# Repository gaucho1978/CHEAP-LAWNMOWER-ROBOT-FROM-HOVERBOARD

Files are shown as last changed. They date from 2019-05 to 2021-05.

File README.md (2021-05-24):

You can control this lawnmower robot with a rc radiocontrol like a big rover, or let it automatically take care of your garden.
You could also replace the radiocontrol with bluetooth receiver conneted on the slave board serial line (reference about this on Florian repository)

The main feature of this lawnmower, with reference to other lawnmower robot products, is that it is able to do its work without a perimeter wire. Compared to other cheap products, it has bigger battery so it is able to take care of really big garden.

Every 24 hours it cuts the garden grass then it returns to the charging station. 

It uses proximity sensors to avoid obstacles and for safety against blade touching (they reveal the distance of the robot from the ground in case someone tries to lift it, in order to stop the blade).

It moves with reference to the start point (the place where the ground station is) knowing which path to follow (i'm planning to save inside the robot the garden morphology or the path) in order to avoid the need of perimeter wire. 
The project is in progress. 

On 12 may 2019 it can only move with rc commands cause iM waiting to receive the sensors and the chassis.

------------------------------
#### MECHANICAL CONSIDERATIONS

The mechanical project is located in the folder LawnMowerMechanicalProject.
These are some images (the base is aluminium and the cover in polycarbonate):
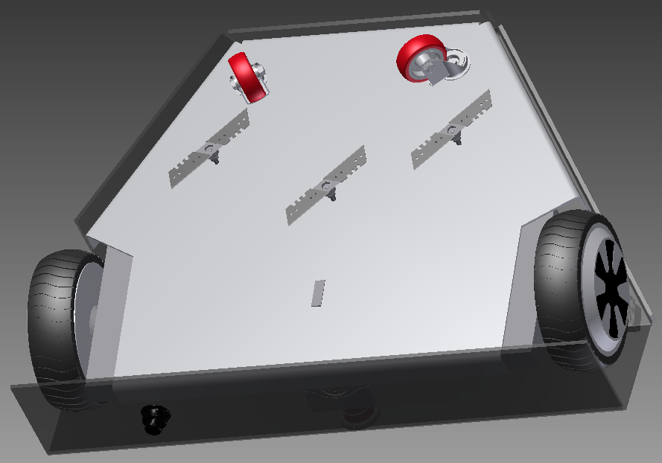
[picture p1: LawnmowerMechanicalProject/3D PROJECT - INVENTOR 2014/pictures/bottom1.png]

otter
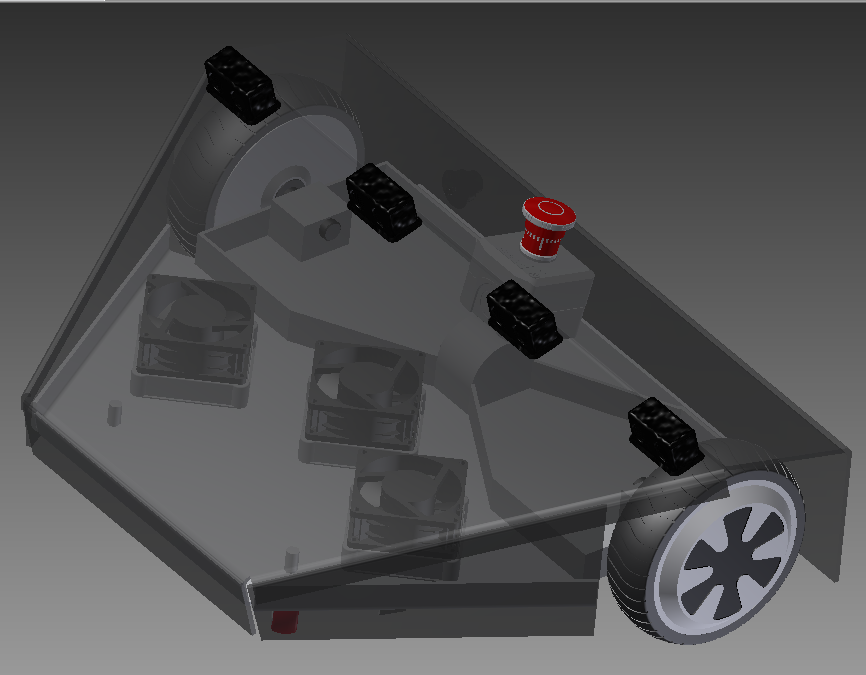
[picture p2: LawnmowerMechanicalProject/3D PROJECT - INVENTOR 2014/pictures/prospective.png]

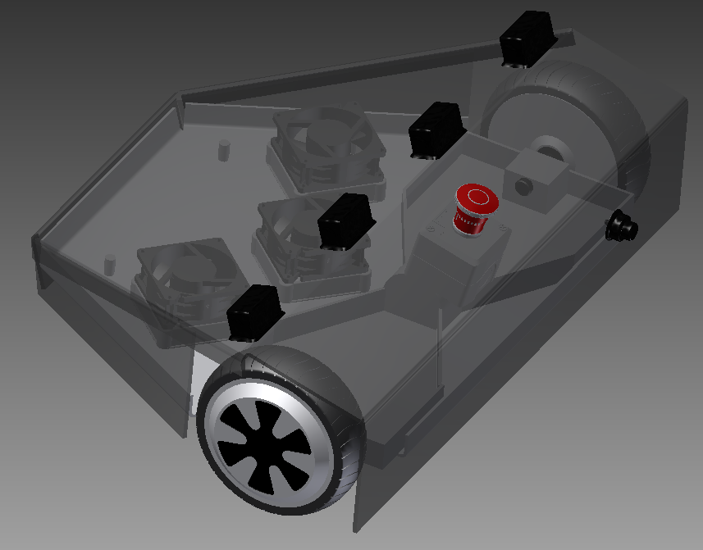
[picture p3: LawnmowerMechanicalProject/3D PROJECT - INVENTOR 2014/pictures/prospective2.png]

otter

- You will find files for manufacturing alluminium plate and polycarbonate cover in the folder:
   LawnMowerMEchanicalProject/FILES FOR MANUFACTURING/PDF FORMAT
- You will fing files for manufacturing plastic supports with 3d printer in the folder:
   LawnMowerMEchanicalProject/FILES FOR MANUFACTURING/3DPrinted supports
- The blade support shall be 3d printed. look ad detailed mechanical drawing to see how to assemble 3dprinted parts.

------------------------------
#### BILL OF MATERIAL - TOTAL COST around 160 EURO
50 EURO - USED HOVERBOARD - https://www.mediaworld.it/product/p-742077/i-bike-kidplay-streetboard-one-hoverboard-6-5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

20 EURO - TURNIGY 9X RADIOCONTROL OR ANY OTHER TYPE OF RC WITH PWM OUTPUT WITH AT LEAST 2 CHANNELS (ONE FOR SPEED AND ONE FOR STEERING)

6 EURO - STLINK V2 PROGRAMMER (TO FLASH HOVERBOARD FIRMWARE) - https://www.ebay.it/itm/352654456738?ViewItem=&item=352654456738

17 EURO - 10 PROXIMITY SENSORS HC-SR04 - https://www.ebay.it/itm/312495306039 https://www.amazon.it/dp/B07MPZR59P/ref=cm_sw_r_cp_apa_glt_i_Q1WTGSVRN5MXQZJ7DQEB?_encoding=UTF8&psc=1

2 EURO - Arduino nano(clone): https://www.ebay.it/itm/322913230315

1 EURO - DCDC(FOR ARDUINO AND/OR BLADE MOTOR): https://www.ebay.it/itm/122201239217

30 EURO - MOTORS FOR BLADES (I REUSED SOME 24V FAN, powering them with modified notebook AC/DC)

30 EURO - 3D PRINTED SUPPORTS FOR BEARING, (I PRINTED THEM FOR FREE WITH MY PRINTER)

1 EURO - FOUR BLADES FOR CUTTER (I FOUND THEM IN A LOCAL HARDWARE STORE (OBI))

10 EURO - POLYCARBONATE OR PLEXIGLASS COVER (I FOUND PIECE OF POLYCARBONATE FOR FREE )

10 EURO - ALUMINIUM OR IRON BASE (I FOUND ALUMINIUM PLATE FOR FREE)

5 EURO - SCREWS AND BOLTS

5 EURO - TWO ROTATING WHEELS 66mm HEIGHT (I FOUND THEM IN A LOCAL CHINESE SHOP)

2 EURO - PANIC BUTTON - https://www.ebay.it/itm/Rosso-fungo-Cap-1-NO-1-NC-ferma-emergenza-Pulsante-interruttore-DPST-660V-10A/123270871363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

------------------------------
#### HOVERBOARD HARDWARE
The hoverboard with 2 boards uses processor GD32F130C8 (instead of STM32F103 used on Niklas hoverboard) 
otter

The hoverboard hardware has two main boards, which are different equipped. They are connected via USART. Additionally there are some LED PCB connected at X1 and X2 which signalize the battery state and the error state. There is an programming connector for ST-Link/V2 and they break out GND, USART/I2C, 5V on a second pinhead.

The reverse-engineered schematics of the mainboards can be found in the folder HoverboardSchematics

In order to use  GPIO represented as "not used" on the hoverboard schematic, you need to solder some zero ohm resistors (or jumpers) (see schematic).

I soldered resistive dividers directly on the pcb as shown on the following image (while on the dwg lawnmower schematic, the resistors are represented as external components). this way the connection to the rc receiver becomes simple as few wires:
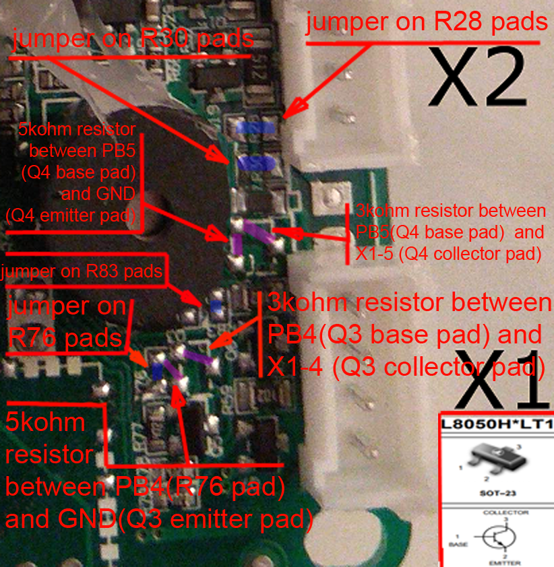
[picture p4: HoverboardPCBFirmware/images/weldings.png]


I REUSED THE HOVERBOARD HARDWARE AS IT IS. I DIDN'T MODIFIED THE FRAME, I JUST ROTATED IT 180 DEGREES.

------------------------------
#### HOVERBOARD FIRMWARE
I started my code from Florian Repository ( https://github.com/flo199213/Hoverboard-Firmware-Hack-Gen2 )

Florian rewrote the firmware for hoverboards composed by 2 boards, starting from Niklas repository ( https://github.com/NiklasFauth/hoverboard-firmware-hack/ )

Niklas rewrote the firmware for hoverboards composed by a big board and sensor boards.

First thing that I've done was to add PWM input to control the robot with a RC receiver, in order to let me do all the functional checks, before to implement automatic navigation algorithm.
I used turnigy rc receiver directly connected to the board, on the unused gpio.

Second thing that i've done was to add PWM output in order to control a ESC connected to a motor. The motor is connected to a blade. 

Every time the robot moves, the blade starts to rotate at constant speed.

The following image shows how the 3 phases changes during rotation. 

Note: A complete rotation of the phases is not a complete rotation of the wheel since there are many inductors inside the motor. 
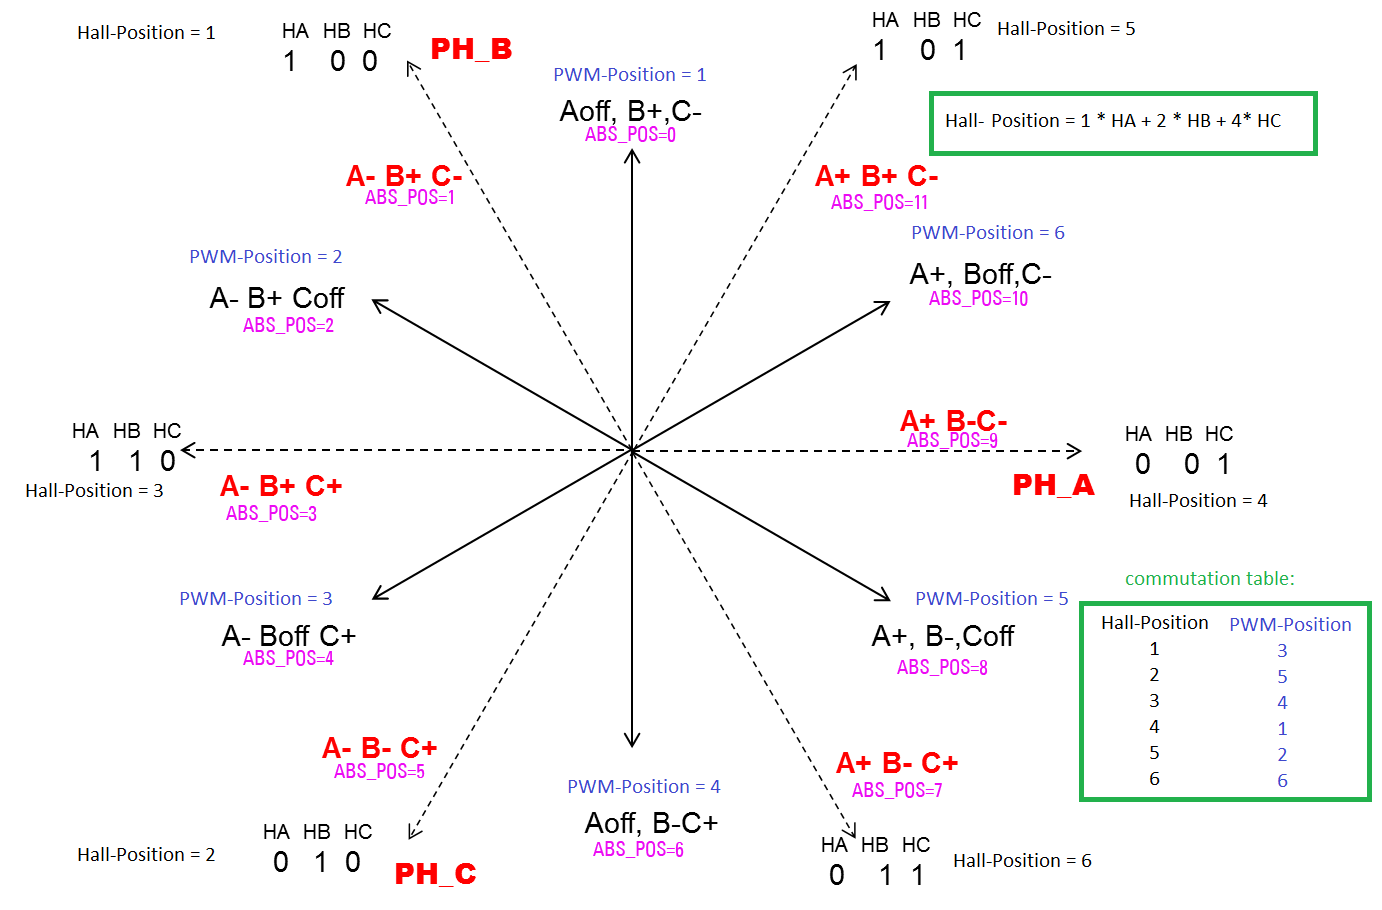
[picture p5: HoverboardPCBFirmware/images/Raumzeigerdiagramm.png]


FIRMWARE STRUCTURE:

-THE FILE "DEFINES" AND "CONFIG" CONTAINS MAIN PARAMETERS 

-THE FILE "IT" CONTAINS TIMING FUNCTIONS AND INTERRUPTS (PERIODIC CHECKS,  SERIAL LINE INTERRUPTS, SYSTEM TICKS)

-THE FILE "BDLC" CONTROLS THE HOVERBOARD MOTORS

-THE FILE "COMMSSTEERINGPWM" RECEIVES THE RC PWM SIGNALS TO MOVE THE HOVERBOARD IN SPEED AND DIRECTION.

-THE FILE "COMMSMASTERSLAVE" SENDS AND RECEIVE DATA BETWEEN MASTER AND SLAVE BOARD

-THE FILE "LED" CONTROLS THE GPIO OUTPUT GENERALLY CONNETED TO LEDS TO SHOW BATTERY STATUS ETC,ETC.

-THE FILE "COMMSACTUATOR"GENERATES THE PWM USED TO CONTROL THE MOTOR CONNECTED TO THE BLADE.

-THE FILE "MAIN" IS THE MAIN LOOP OF THE HOVERBOARD FIRMWARE THAT CALLS ALL THE ROUTINES IN SEQUENCE.

------------------------------
#### FLASHING
The firmware is built with Keil (free up to 32KByte). To build the firmware, open the Keil project file which is includes in repository. On the board, close to ARM processor, there is a debugging header with GND, 3V3, SWDIO and SWCLK. Connect GND, SWDIO and SWCLK to your SWD programmer, like the ST-Link V2.

- If you never flashed your mainboard before, the controller is locked. To unlock the flash, use STM32 ST-LINK Utility or openOCD.
- To flash the processor, use the STM32 ST-LINK Utility as well, ST-Flash utility or Keil by itself.
- Hold the powerbutton while flashing the firmware, as the controller releases the power latch and switches itself off during flashing

NOTE: I USE TO UNPLUG THE HOVERBOARD BATTERY AND TO PLUG THE STLINK PROGRAMMER (INCLUDED 3,3VOLT PIN), THEN TO FLASH THE FW USING KEIL. THIS WAY YOU DON'T NEED TO LEAVE PRESSED THE POWER BUTTON.

NOTE2: ONE BOARD IS MASTER THE OTHER IS SLAVE. BEFORE TO FLASH THE FW, SET THE FIRMWARE AS MASTER OR SLAVE IN THE CONFIG.H AND RECOMPILE THE FIRMWARE.

------------------------------
#### COMMUNITY
there is a Telegram group as a free discussion platform about Hoverboards MODS. You can find it here: https://t.me/joinchat/BHWO_RKu2LT5ZxEkvUB8uw

------------------------------
#### NEXT THINGS THAT I WILL DO: 
- add sensors and interlocks to algorithm,
- create a docking station for automatic recharge, 
- realize the mechanical structure, 
- implement safety for automatic stopping blade 
- implement automatic navigation algorithm.

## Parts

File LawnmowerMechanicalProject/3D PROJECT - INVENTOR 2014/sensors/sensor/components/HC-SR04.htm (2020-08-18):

Autodesk Inventor Translation Report | domenica 12 aprile 2020 (13:39)
Source File: | C:\Users\GauchoHP\Downloads\HC-SR04.stp
Translator Type: | STEP | Sending System: | DEX
Author: | Unknown | Translation Time: | 00:00:09
Options
Import Type: | N/A
Entity Types to Import: | Solids, Surfaces, Wires, Points
Import into Repair Environment: | Yes
Import Assembly as Single Part: | No
Create Surfaces As: | Single Composite Feature
Check Parts during Load: | No
Auto Stitch: | No
Enable Advanced Healing: | N/A
+/- | Name | Inventor File | Status
[ ] | HC-SR04.iam | C:\Users\GauchoHP\Downloads\Imported Components\HC-SR04\HC-SR04.iam | Successful
[+] [-] | Board.ipt | C:\Users\GauchoHP\Downloads\Imported Components\HC-SR04\Board.ipt | Warning
Severity | Entity Id | Message
Warning | 64531 | Some Surfaces have been simplified
[ ] | SOT23.ipt | C:\Users\GauchoHP\Downloads\Imported Components\HC-SR04\SOT23.ipt | Successful
[+] [-] | SOIC16 narrow.ipt | C:\Users\GauchoHP\Downloads\Imported Components\HC-SR04\SOIC16 narrow.ipt | Warning
Severity | Entity Id | Message
Warning | 260 | Some Surfaces have been simplified
[ ] | Crystal Oscillator (SMD).ipt | C:\Users\GauchoHP\Downloads\Imported Components\HC-SR04\Crystal Oscillator (SMD).ipt | Successful
[+] [-] | 0603 Resistor.ipt | C:\Users\GauchoHP\Downloads\Imported Components\HC-SR04\0603 Resistor.ipt | Warning
Severity | Entity Id | Message
Warning | 259 | Some Surfaces have been simplified
Warning | 259 | Sliver faces have been removed
[ ] | 0603 Capacitor.ipt | C:\Users\GauchoHP\Downloads\Imported Components\HC-SR04\0603 Capacitor.ipt | Successful
[ ] | Transducer.ipt | C:\Users\GauchoHP\Downloads\Imported Components\HC-SR04\Transducer.ipt | Successful
[ ] | Mesh.ipt | C:\Users\GauchoHP\Downloads\Imported Components\HC-SR04\Mesh.ipt | Successful

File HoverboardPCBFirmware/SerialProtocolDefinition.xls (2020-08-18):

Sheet: Messages
Direction | Byte Count | 0 | 1 | 2 | 3 | 4 | 5 | 6 | 7 | 8 | 9 | 10 | Note
Remote Serial Port → Master Board | 3-:-9 | / | cmd | ± | Value |  |  |  |  | \r |  |  | This message uses only ASCII characters and it is used as debug port Bytes from 2 to 7 are optional, used only in movement commands cmd: See CMD LEGEND sheet
 |  | char | char | char | char1 | char2 | char3 | char4 | char5 | char
Master Board→ Remote Serial Port | for returned message see CMD LEGEND sheet
Master Board→ Slave Board | 10 | / | SPEED |  | ID | VALUE |  | Bits | CRC |  | \n |  | SPEED: is the SPEED value in mm/sec to set on the Slave motor Identifier+Value: See ID Legend sheet Bits: See Bits Legend sheet CRC: checksum of the transmitted data
 |  | char | int16 |  | uint8 | int16 |  | uint8 | uint16 |  | char
Slave Board → Master Board | 5 | / | Bits | CRC |  | \n
 |  | char | uint8 | uint16 |  | char
Slave Board→ Remote Serial port | 11 | / | ID |  | 0 | ± | Value |  |  |  |  | \n | ID, ReadWrite and VALUE are ascii characters. ID: from 00 to 99 (see ID Legend sheet) ReadWrite: Read=0, Write=1 ±Value: from -10000 to 10000
 |  | char | char1 | char2 | uint8 | char | char1 | char2 | char3 | char4 | char5 | char
Remote Serial port → Slave Board | 11 | / | ID |  | Read Write | ± | Value |  |  |  |  | \n
 |  | char | char1 | char2 | uint8 | char | char1 | char2 | char3 | char4 | char5 | char

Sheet: CMD Legend
Master Board ↔ Remote Serial Port CMD legend
CMD | Meaning | Note
h | Prints Commands Legend. A kind of Help | to enable these commands ensure that TERMINAL_ENABLED is defined in config.h
l | Prints IMU log table, with gyroscope values, accelerometer values, time, roll and pitch values, aquired in a small buffer. Note: it is a lowercase L, not a uppercase I
s | Prints current speed and steer values
m | Moves forward the robot by the number of millimeters specified in Value parameter. Positive values between 00001 and 32767 moves it forward. Negative values between -00001 and -32767 moves it backward. Done! Is returned when movement is complete.
t | Turns the robot by an angle in degrees specified in Value parameter. Positive values between 00001 and 00360 rotates it clockwise(right). Negative values between -00001 and -00360 rotates it counter-clockwise(left). Note: Rotation is actuated simultaneously on both wheels Done! Is returned when movement is complete.
p | apply proportional constant (x10000) of the PID control. This data will be automatically sent to slave wheel. | to enable these commands ensure that TERMINAL_ENABLED_PID_TUNING is defined in config.h
i | apply integral constant (x10000) of the PID control. This data will be automatically sent to slave wheel.
d | apply derivative constant (x10000) of the PID control. This data will be automatically sent to slave wheel.

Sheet: ID Legend
Slave Board ↔ Remote Serial Port Identifiers legend |  |  |  |  |  | Master Board->Slave Board Identifiers legend
Read | Write | ID | Meaning | Location | Range | ID | Meaning | Location | Range
X |  | 0 | Battery Voltage | Master | Value*100 | 0 | Current | Master | Value*100
X |  | 1 | Current | Master | Value*100 | 1 | battery Voltage | Master | Value*100
X |  | 2 | Current | Slave | Value*100 | 2 | Real Speed | Master | Value*100
X |  | 3 | Real Speed | Master | Value*100 | 3 | Distance | Master | millimeters
X |  | 4 | Real Speed | Slave | Value*100 | 4 | remaining steps | Master | units
X | X | 5 | Beeps backwards | Master | Off=0, On=1 | 5 | Proportional PID | Master | Value*1000
X | X | 6 | Lower led | Master | Off=0, On=1 | 6 | Integral PID | Master | Value*1000
X | X | 7 | Upper led | Master | Off=0, On=1 | 7 | Differential PID | Master | Value*1000
X | X | 8 | LED Hue | Slave | 0-764
X | X | 9 | LED Saturation | Slave | 0-128
X | X | 10 | LED Brightness | Slave | 0-63
X | X | 11 | LED Mode | Slave | LED_OFF = 0, LED_HSB = 1, LED_HSB_BLINK = 2, LED_HSB_FADE = 3, LED_HSB_STROBE = 4
X | X | 12 | LED Fading Speed | Slave | 200-1000
X | X | 13 | LED Blink Speed | Slave | 700-2400
X | X | 14 | LED Strobe Speed | Slave | 0-1000

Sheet: Bits Legend
Bits Legend
Direction | Bit Number | Description | Note
Master->Slave | Bit7 | The Master tells to the slave board to Shut Off (1=shutoff)
 | Bit6 | Not Used
 | Bit5 | Not Used
 | Bit4 | Not Used
 | Bit3 | Not Used
 | Bit2 | Not Used
 | Bit1 | Charge status: If 1 is received, it sets digital output PA15 (green led) If 0 is received, it sets digital output PB3 (red led) | 1= Not in charge 0= In charge
 | Bit0 | Enable: If 1 is received, it enables motor control
Slave->Master | Bit7 | Not Used
 | Bit6 | Not Used
 | Bit5 | Not Used
 | Bit4 | moveByStepsCompleted: raised when Slave board completes a movement by steps | master board check this bit to know when movement by steps (requested with Identifier 3 + value) is completed on the slave board. It slave board is moving with pwm parameter, this bit has no meaning.
 | Bit3 | Beeps Backwards:1=True, 0=False | Slave board receives this from Remote port
 | Bit2 | MosfetOut: if 1 is received, it is set Mosfet Output (digital output PC13) | Not used in slave board
 | Bit1 | Lower Led: If 1 is received, Master board lights Lower Led(digital output PA0) | Slave board receives this from Remote port
 | Bit0 | Upper Led: If 1 is received, Master board lights Upper Led(digital output PA1) | Slave board receives this from Remote port

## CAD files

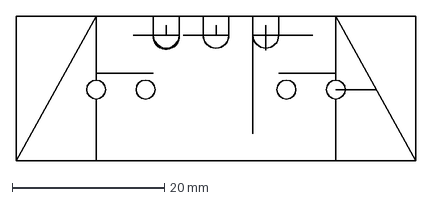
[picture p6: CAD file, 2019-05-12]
LawnmowerMechanicalProject/3D PROJECT - INVENTOR 2014/lama/aaaaaaaaa.dxf
52.5 x 19.0 mm

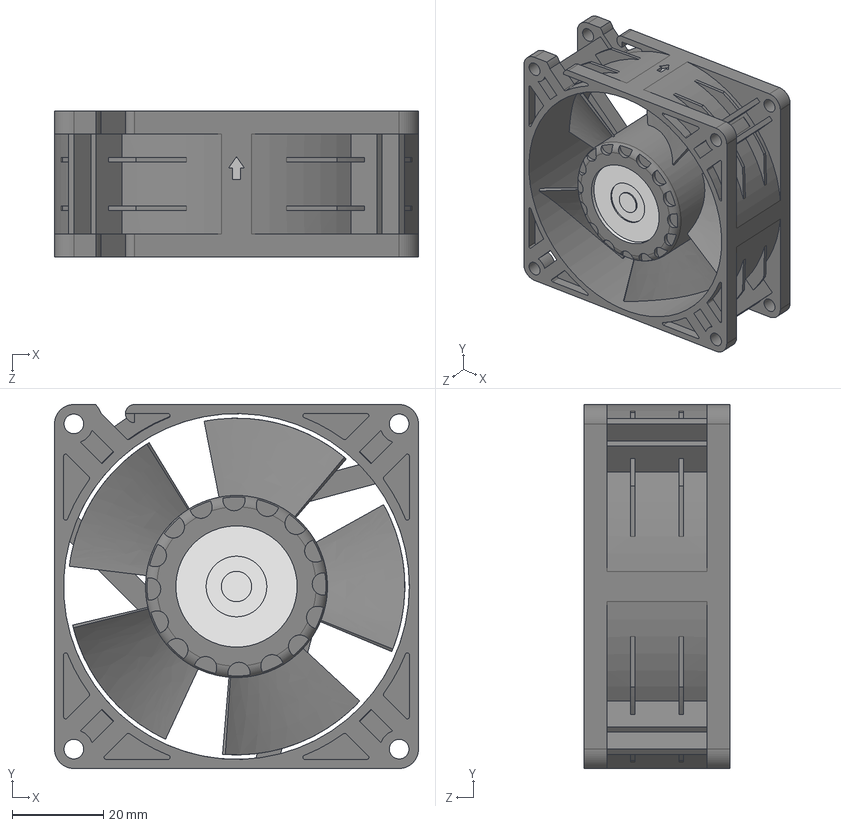
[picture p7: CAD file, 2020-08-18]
LawnmowerMechanicalProject/3D PROJECT - INVENTOR 2014/motor with blades/motor.step
80.0 x 80.0 x 32.0 mm
Fan_8312_NL_ebm-papst_8312 NL_ebm-papst
Fan-House_8312_NL_ebm-papst_8312 NL_ebm-papst

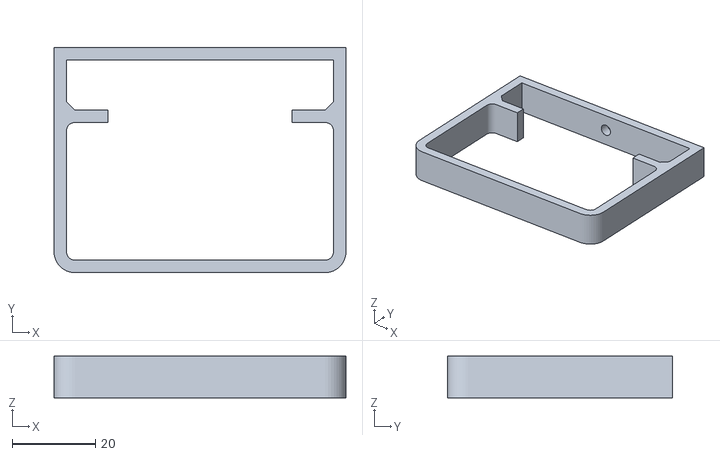
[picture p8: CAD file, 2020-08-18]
LawnmowerMechanicalProject/FILES FOR MANUFACTURING/3DPrinted supports/dcdcSupport.stl
70.0 x 54.0 x 10.0

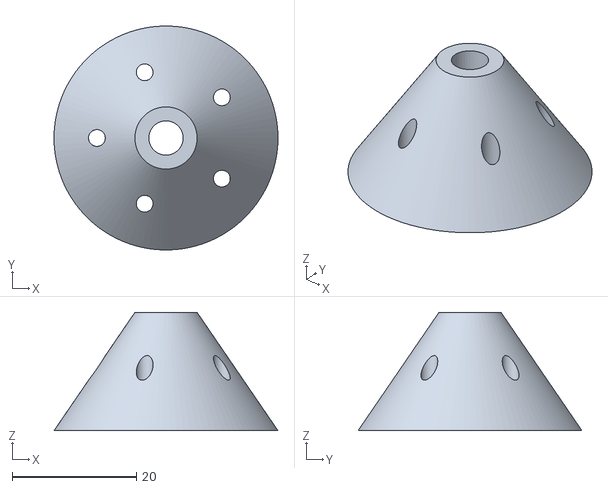
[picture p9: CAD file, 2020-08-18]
LawnmowerMechanicalProject/FILES FOR MANUFACTURING/3DPrinted supports/motorSupportShaft.stl
36.0 x 36.0 x 19.0

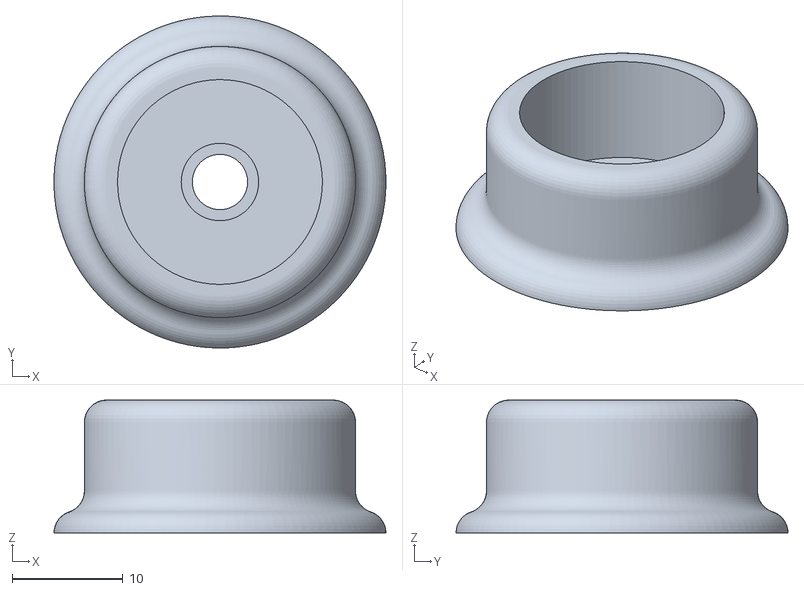
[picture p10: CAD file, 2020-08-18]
LawnmowerMechanicalProject/FILES FOR MANUFACTURING/3DPrinted supports/powerButtonPart2.stl
30.0 x 30.0 x 12.0

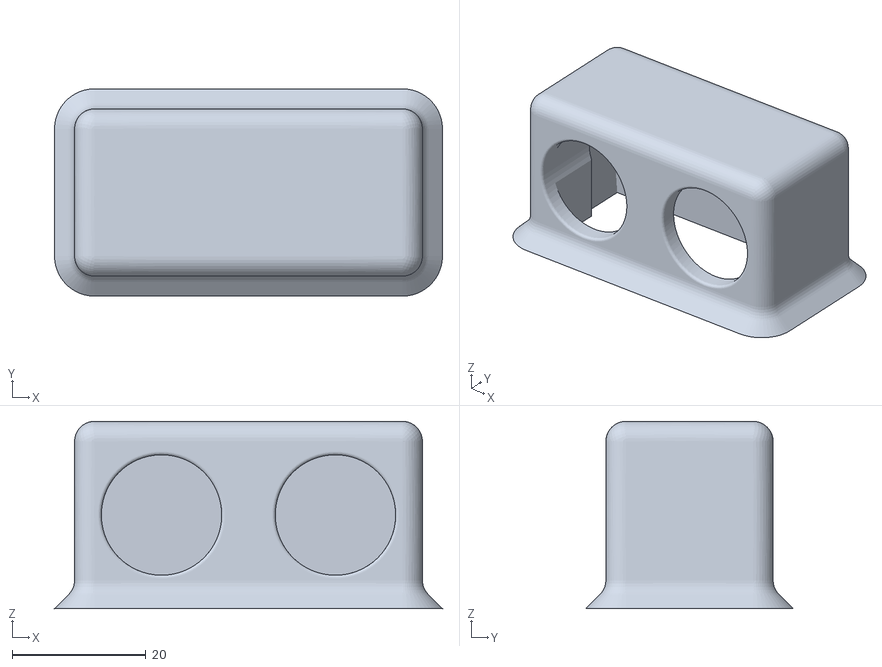
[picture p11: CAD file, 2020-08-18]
LawnmowerMechanicalProject/FILES FOR MANUFACTURING/3DPrinted supports/ultrasonicSensorSupport.stl
58.0 x 31.0 x 28.0

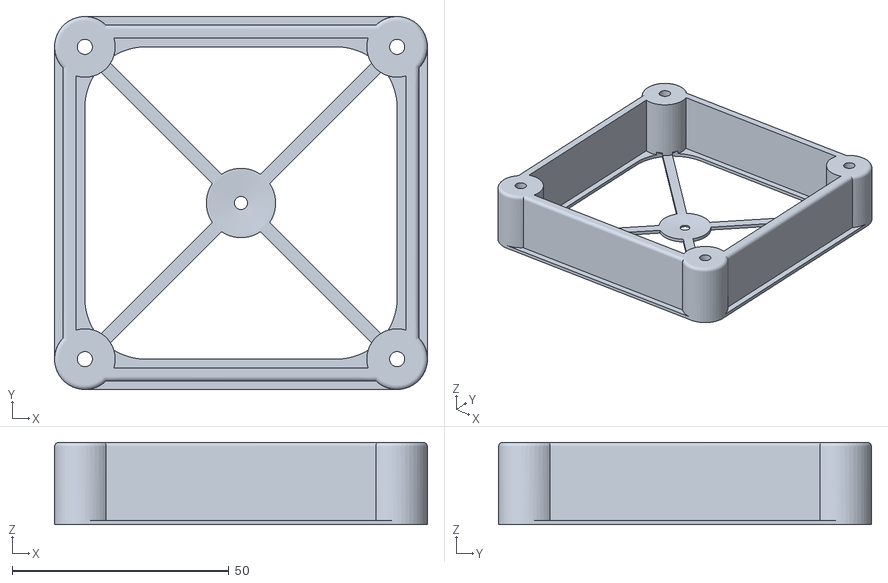
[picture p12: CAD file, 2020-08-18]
LawnmowerMechanicalProject/FILES FOR MANUFACTURING/3DPrinted supports/motorSupportSpacer.stl
86.0 x 86.0 x 19.0

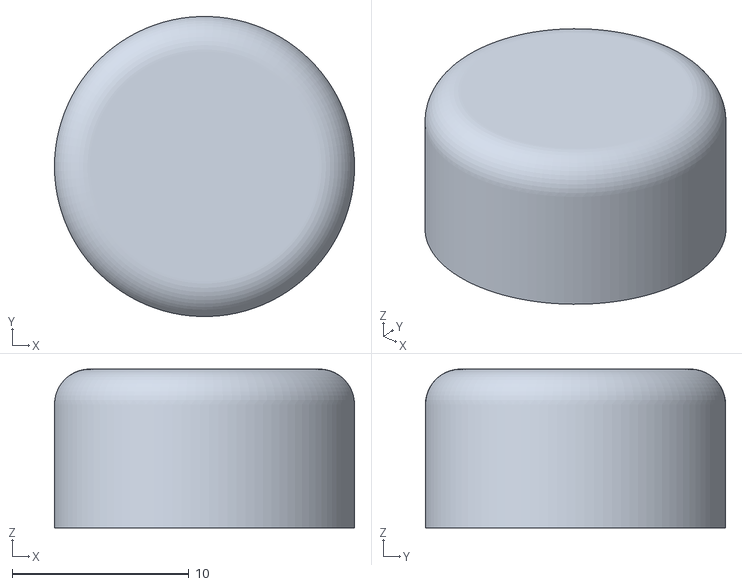
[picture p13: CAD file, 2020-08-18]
LawnmowerMechanicalProject/FILES FOR MANUFACTURING/3DPrinted supports/powerButtonPart1.stl
17.0 x 17.0 x 9.00

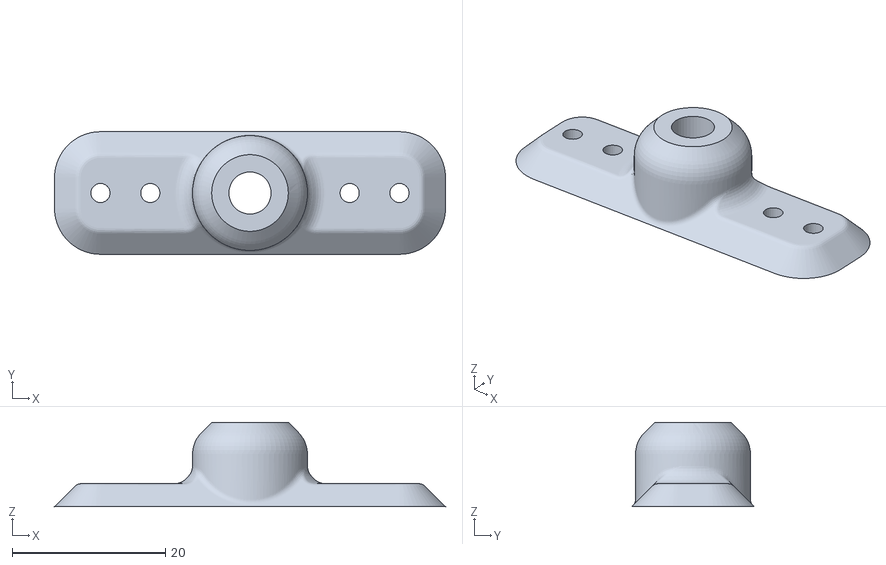
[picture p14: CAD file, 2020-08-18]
LawnmowerMechanicalProject/FILES FOR MANUFACTURING/3DPrinted supports/support_for_2_blades.stl
51.0 x 16.0 x 11.0

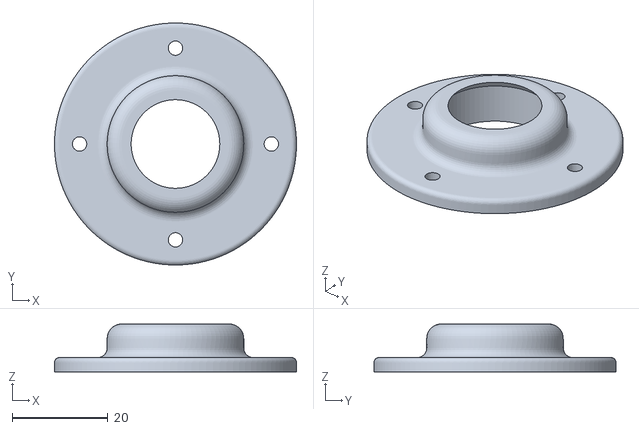
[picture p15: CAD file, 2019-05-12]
LawnmowerMechanicalProject/FILES FOR MANUFACTURING/3DPrinted supports/supportoCuscinettoAlto.stl
50.5 x 50.5 x 10.0

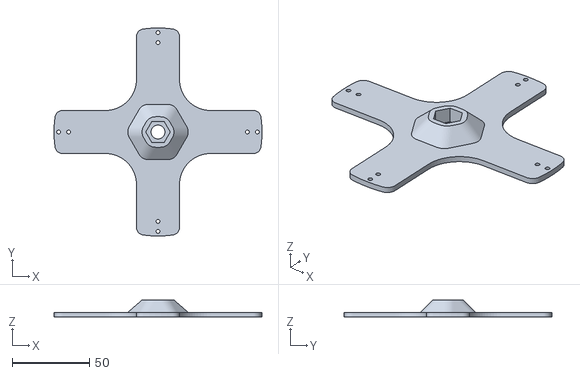
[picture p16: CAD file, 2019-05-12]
LawnmowerMechanicalProject/FILES FOR MANUFACTURING/3DPrinted supports/bladeSupport.stl
134.9 x 134.9 x 11.0

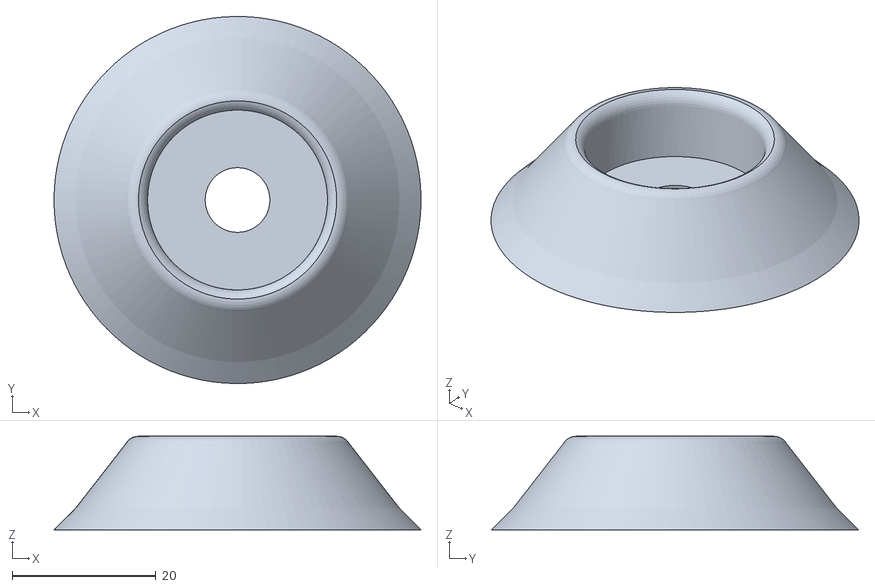
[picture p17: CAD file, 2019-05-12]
LawnmowerMechanicalProject/FILES FOR MANUFACTURING/3DPrinted supports/boltCap.stl
51.0 x 51.0 x 13.0

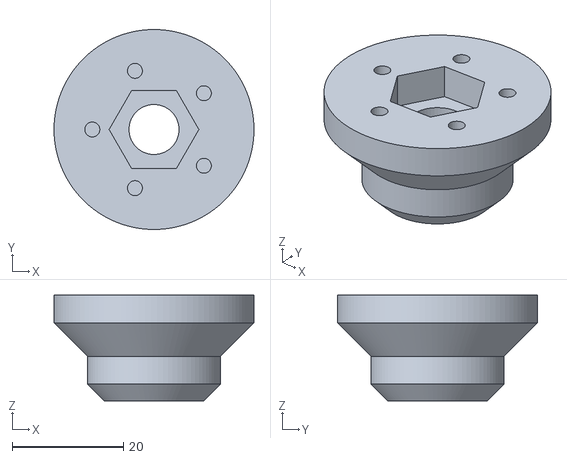
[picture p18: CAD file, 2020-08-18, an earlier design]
LawnmowerMechanicalProject/3D PROJECT - INVENTOR 2014/motor with blades/old/old3_modified_fan/motorSupportNew1 modified2.stl
36.0 x 36.0 x 19.0

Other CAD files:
LawnmowerMechanicalProject/2D DRAWINGS - AUTOCAD FORMAT/sponda laterale policarbonato.dwg
LawnmowerMechanicalProject/Ultrasonic Sensors Area Coverage/topView.dwg
LawnmowerMechanicalProject/2D DRAWINGS - AUTOCAD FORMAT/PIASTRA2D_EN.dwg
LawnmowerMechanicalProject/2D DRAWINGS - AUTOCAD FORMAT/POLICARBONATO2D_EN.dwg
LawnmowerMechanicalProject/3D PROJECT - INVENTOR 2014/OldVersions/tosaerba.0034.iam
LawnmowerMechanicalProject/3D PROJECT - INVENTOR 2014/aluminium base plate/piastra.ipt
LawnmowerMechanicalProject/3D PROJECT - INVENTOR 2014/cover plexiglass/coverPolicarbonato2.ipt
LawnmowerMechanicalProject/3D PROJECT - INVENTOR 2014/cover plexiglass/sponda laterale policarbonato.ipt
LawnmowerMechanicalProject/3D PROJECT - INVENTOR 2014/external DC_DC_power_supply support/dcdcSupport.ipt
LawnmowerMechanicalProject/3D PROJECT - INVENTOR 2014/hoverboard/base/hoverboard plate.ipt
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

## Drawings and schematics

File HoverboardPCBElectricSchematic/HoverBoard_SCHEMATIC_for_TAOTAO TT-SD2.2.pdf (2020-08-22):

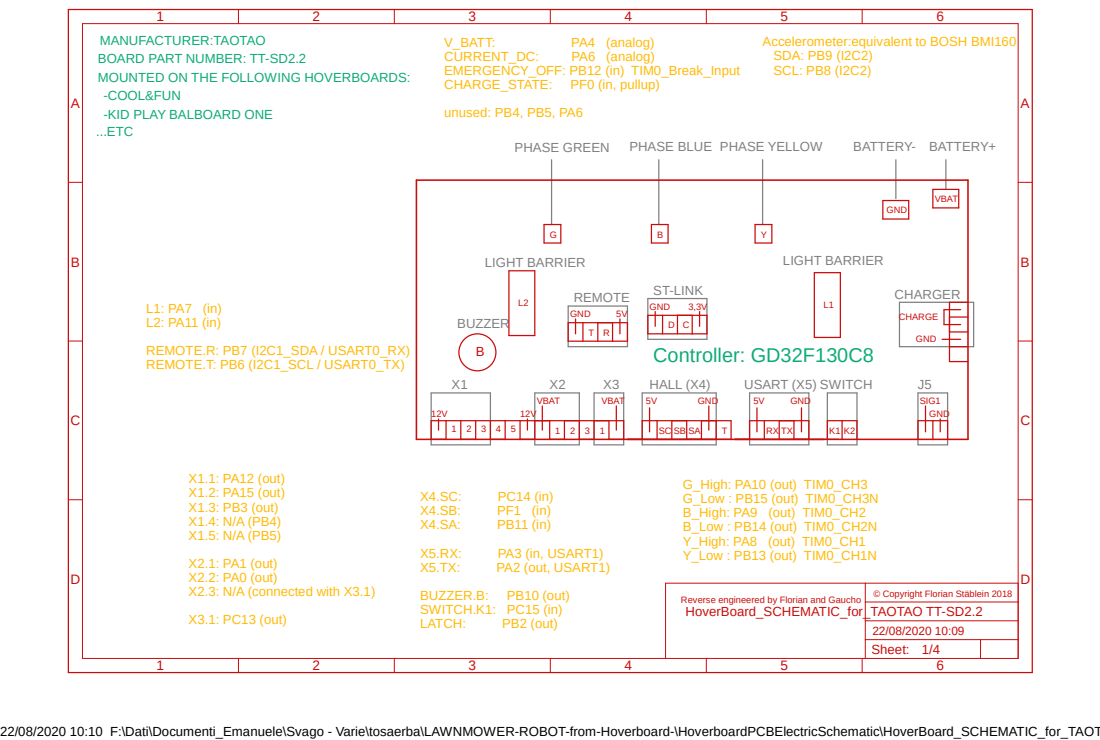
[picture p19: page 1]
HALL (X4); USART (X5) SWITCH; REMOTE; ST-LINK; CHARGER; PHASE GREEN; PHASE BLUE PHASE YELLOW; LIGHT BARRIER; BATTERY- BATTERY+; BUZZER; VBAT; GND; SIG1 GND; CHARGE; Sheet:; Controller: GD32F130C8; X1.1: PA12 (out) X1.2: PA15 (out) X1.3: PB3 (out) X1.4: N/A (PB4) X1.5: N/A (PB5); X2.1: PA1 (out) X2.2: PA0 (out) X2.3: N/A (connected with X3.1); X3.1: PC13 (out); PA3 (in, USART1); PA2 (out, USART1); BUZZER.B:; PB10 (out); SWITCH.K1: PC15 (in); LATCH:; PB2 (out)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

MANUFACTURER:TAOTAO
BOARD PART NUMBER: TT-SD2.2
MOUNTED ON THE FOLLOWING HOVERBOARDS:
-COOL&FUN
-KID PLAY BALBOARD ONE
...ETC

Accelerometer:equivalent to BOSH BMI160
SDA: PB9 (I2C2)
SCL: PB8 (I2C2)

© Copyright Florian Stäblein 2018

Reverse engineered by Florian and Gaucho
HoverBoard_SCHEMATIC_for_TAOTAO TT-SD2.2

22/08/2020 10:10 F:\Dati\Documenti_Emanuele\Svago - Varie\tosaerba\LAWNMOWER-ROBOT-from-Hoverboard-\HoverboardPCBElectricSchematic\HoverBoard_SCHEMATIC_for_TAOTAO TT-SD2.2.sch (Sheet: 1/4)

## HALL

## USART

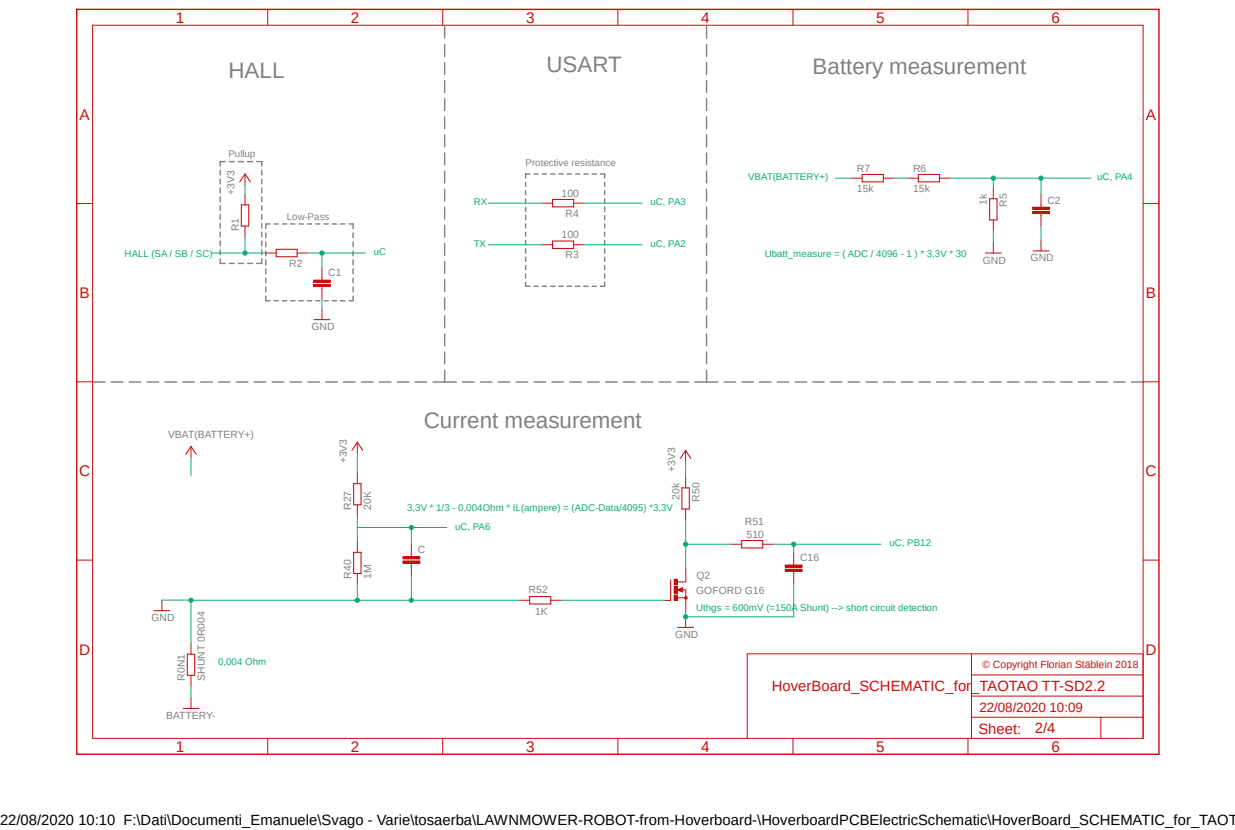
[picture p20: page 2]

3,3V * 1/3 - 0,004Ohm * IL(ampere) = (ADC-Data/4095) *3,3V

GOFORD G16
Uthgs = 600mV (=150A Shunt) --> short circuit detection

22/08/2020 10:10 F:\Dati\Documenti_Emanuele\Svago - Varie\tosaerba\LAWNMOWER-ROBOT-from-Hoverboard-\HoverboardPCBElectricSchematic\HoverBoard_SCHEMATIC_for_TAOTAO TT-SD2.2.sch (Sheet: 2/4)

X1-1 | X1-2 | X1-3 | X1-4

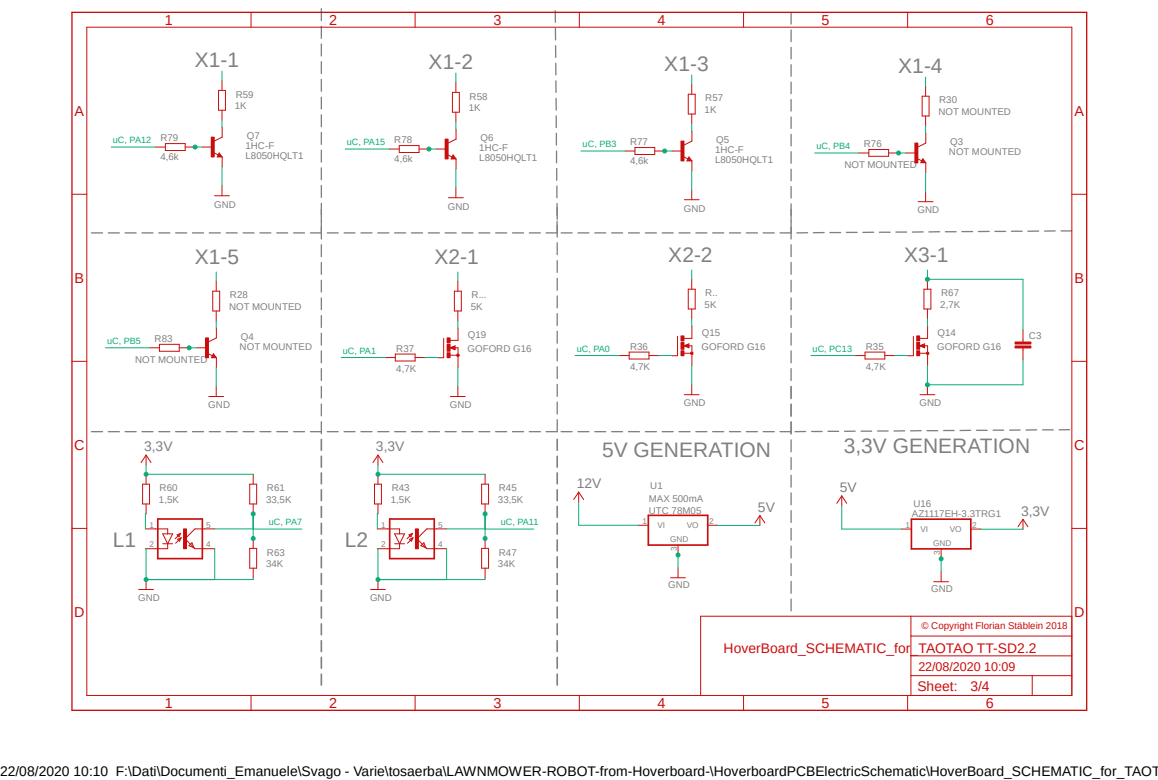
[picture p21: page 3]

22/08/2020 10:10 F:\Dati\Documenti_Emanuele\Svago - Varie\tosaerba\LAWNMOWER-ROBOT-from-Hoverboard-\HoverboardPCBElectricSchematic\HoverBoard_SCHEMATIC_for_TAOTAO TT-SD2.2.sch (Sheet: 3/4)

## CHARGER INPUT

## "REMOTE" SERIAL PORT

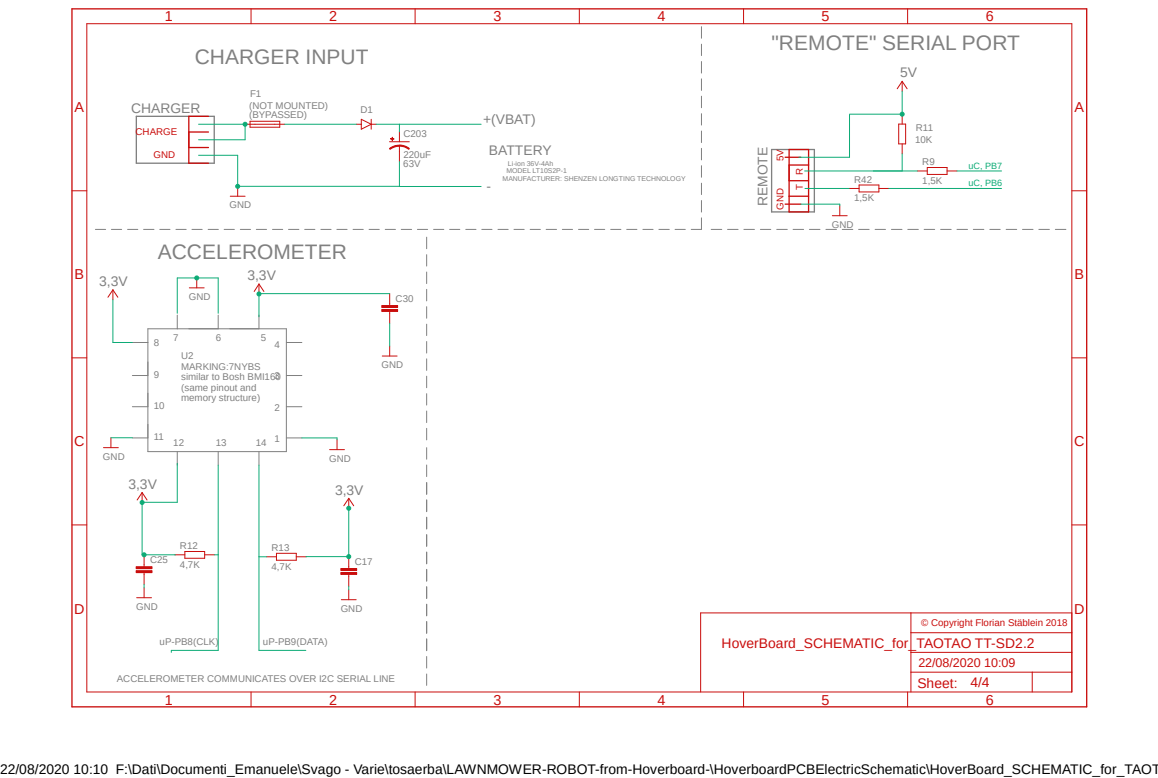
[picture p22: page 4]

MANUFACTURER: SHENZEN LONGTING TECHNOLOGY GND

ACCELEROMETER COMMUNICATES OVER I2C SERIAL LINE

22/08/2020 10:10 F:\Dati\Documenti_Emanuele\Svago - Varie\tosaerba\LAWNMOWER-ROBOT-from-Hoverboard-\HoverboardPCBElectricSchematic\HoverBoard_SCHEMATIC_for_TAOTAO TT-SD2.2.sch (Sheet: 4/4)

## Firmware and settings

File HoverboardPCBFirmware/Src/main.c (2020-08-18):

//defines the main program loop

#define ARM_MATH_CM3

#include "gd32f1x0.h"

#include "../Inc/setup.h"
#include "../Inc/defines.h"
#include "../Inc/config.h"
#include "../Inc/it.h"
#include "../Inc/bldc.h"
#include "../Inc/commsMasterSlave.h"
#include "../Inc/commsRemote.h"
#include "../Inc/commsSteeringPWM.h"
#include "../Inc/commsInterlocks.h"
#include "../Inc/commsBluetooth.h"
#include "../Inc/commsAccelerometer.h"
#include "../Inc/navigator.h"

#include "stdio.h"
#include "stdlib.h"
#include "string.h"
#include <math.h>     
#include "arm_math.h" 

#ifdef MASTER

	//int32_t steer = 0; 												// global variable for steering. -1000 to 1000
	//int32_t speed = 0; 												// global variable for speed.    -1000 to 1000
	int16_t speed_mm_per_second_MasterWheel=(int16_t)0;						// global variable for speed in mm per second -6000 +6000 (21,6km/h)
	int16_t speed_mm_per_second_SlaveWheel=(int16_t)0;						// global variable for speed in mm per second -6000 +6000 (21,6km/h)
	int16_t speed_mm_per_second=(int16_t)0;						// global variable for speed in mm per second -6000 +6000 (21,6km/h)
	
	int16_t steerAngle = 0;  //angle pf steer between 180 and 0 degrees. 90 degrees to go straight
		
	int32_t actuatorSpeed = 0;								// actuator(lawnmower motor blade) speed. 0 to 1000
	
	float logImuArray[400]; 									//array of array for logging purposes
	int16_t logImuArrayCurrentIndex=0; 				//index for log file
	
	float pitchAngle=0;
	float rollAngle=0;
	float yawAngle=0;
	
	bool recordAccelerometerLog=FALSE;
	bool printAccelerometerLog=FALSE;
	
	FlagStatus panicButtonPressed = SET;			//global variable. RESET when pressed.
	FlagStatus it_is_Raining = RESET;					//global variable. SET when raining.
	
	FlagStatus activateWeakening = RESET;			// global variable for weakening
	FlagStatus beepsBackwards = RESET;  			// global variable for beeps backwards
				
	extern uint8_t buzzerFreq;    						// global variable for the buzzer pitch. can be 1, 2, 3, 4, 5, 6, 7...
	extern uint8_t buzzerPattern; 						// global variable for the buzzer pattern. can be 1, 2, 3, 4, 5, 6, 7...
				
	extern float batteryVoltage; 							// global variable for battery voltage
	extern float currentDC; 									// global variable for current dc
	extern float realSpeed_mm_per_second; 									// global variable for real Speed
	extern bool moveBySteps;									//global variable for movements controlled in steps(=1) or classic movements controlled by speed and steer (=0)
	extern bool moveByStepsCompleted;					//global variable. 1= movement completed.
	extern int16_t remainingSteps;
	extern FlagStatus timedOut;								// Timeoutvariable set by timeout timer
	
	bool robotReversed=FALSE;
	
	uint32_t inactivity_timeout_counter = 0;	// Inactivity counter
	uint32_t steerCounter = 0;								// Steer counter for setting update rate

	void ShowBatteryState(uint32_t pin);
	void BeepsBackwards(FlagStatus beepsBackwards);
	void ShutOff(void);
	

		extern float PID_PARAM_KP;
		extern float PID_PARAM_KI;
		extern float PID_PARAM_KD;		
#endif

const float lookUpTableAngle[181] =  {
  -1,
  -0.937202577,
  -0.878193767,
  -0.822607884,
  -0.770124422,
  -0.720461266,
  -0.673369096,
  -0.628626737,
  -0.58603728,
  -0.545424828,
  -0.506631749,
  -0.46951635,
  -0.433950895,
  -0.399819915,
  -0.367018754,
  -0.335452314,
  -0.30503398,
  -0.275684674,
  -0.24733204,
  -0.219909731,
  -0.193356783,
  -0.167617063,
  -0.142638788,
  -0.118374098,
  -0.094778672,
  -0.071811398,
  -0.049434068,
  -0.027611115,
  -0.006309372,
  0.014502141,
  0.03485241,
  0.054768601,
  0.074276213,
  0.093399224,
  0.112160212,
  0.130580478,
  0.148680146,
  0.166478264,
  0.183992885,
  0.201241154,
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
};


//----------------------------------------------------------------------------
// MAIN function
//----------------------------------------------------------------------------
int main (void){
#ifdef MASTER
	FlagStatus enable = RESET;
	FlagStatus enableSlave = RESET;
	FlagStatus chargeStateLowActive = SET;
	
	int16_t sendSlaveValue = 0;
	uint8_t sendSlaveIdentifier = 0;
	int8_t index = 8;
  //int16_t pwmSlave = 0;
	//int16_t pwmMaster = 0;
	//int16_t scaledSpeed = 0;
	//int16_t scaledSteer  = 0;
	//float expo = 0;

	float xScale = 0;
#endif
	
	//SystemClock_Config();
  SystemCoreClockUpdate();
  SysTick_Config(SystemCoreClock / 100);
	
	// Init watchdog
	if (Watchdog_init() == ERROR)
	{
		// If an error accours with watchdog initialization do not start device
		while(1);
	}
	
	// Init Interrupts
	Interrupt_init();
	
	// Init timeout timer
	TimeoutTimer_init();
	
	// Init GPIOs
	GPIO_init();
	
	// Activate self hold direct after GPIO-init
	gpio_bit_write(SELF_HOLD_PORT, SELF_HOLD_PIN, SET);

	// Init usart master slave
	USART_MasterSlave_init();

	#ifdef MASTER	
		//init i2c that communicates with accelerometer
		I2C_IMU_init();
	#endif
	// Init ADC
	ADC_init();
	
	// Init PWM
	PWM_init();

	#ifdef SLAVE
		PID_init();
	#endif
	// Device has 1,6 seconds to do all the initialization
	// afterwards watchdog will be fired
	fwdgt_counter_reload();

	// Init remote usart
	USART_REMOTE_COM_init();

#ifdef MASTER
	// Startup-Sound
	for (; index >= 0; index--)
	{
    buzzerFreq = index;
    Delay(10);
  }
  buzzerFreq = 0;

	// Wait until button is pressed
	while (gpio_input_bit_get(BUTTON_PORT, BUTTON_PIN))
	{
		// Reload watchdog while button is pressed
		fwdgt_counter_reload();
	}
	
#endif

  while(1)
	{
#ifdef MASTER
		steerCounter++;	
		Send_Data_over_REMOTE_serialPort_of_MasterBoard();
		
		// Read charge state
		chargeStateLowActive = gpio_input_bit_get(CHARGE_STATE_PORT, CHARGE_STATE_PIN);
		// Enable is depending on charger is connected or not
		enable = chargeStateLowActive;
		
		//mainLoopPeriodMilliseconds=(halfMillisecondsCount+1)/2;
		//halfMillisecondsCount=0;
		
		if(moveBySteps){ //movements controlled in number of steps forward or backward
			// Reset the pwm timout to avoid stopping motors
			ResetTimeout();
			// do not shutdown if movement by steps is in progress
			inactivity_timeout_counter = 0;
			
			
		}else{ //classic movements controlled by speed and steer
			
			// Calculate expo rate for less steering with higher speeds
			//expo = MAP((float)ABS(speed), 0, 1000, 1, 0.5);
			
			// Each speedvalue or steervalue between 50 and -50 means absolutely no pwm
			// -> to get the device calm 'around zero speed'
			//scaledSpeed = speed < 50 && speed > -50 ? 0 : CLAMP(speed, -1000, 1000) * SPEED_COEFFICIENT;
			//scaledSteer = steer < 50 && steer > -50 ? 0 : CLAMP(steer, -1000, 1000) * STEER_COEFFICIENT * expo;
			
			
			
			// Map to an angle of 180 degress to 0 degrees for array access (means angle -90 to 90 degrees)
			//steerAngle = MAP((float)scaledSteer, -1000, 1000, 180, 0);
			xScale = lookUpTableAngle[(uint16_t)steerAngle];

				
				// Mix steering and speed value for right and left speed
				if(steerAngle >= 90){
					speed_mm_per_second_MasterWheel= CLAMP(speed_mm_per_second,-1000,1000);
					speed_mm_per_second_SlaveWheel = CLAMP(speed_mm_per_second / xScale,-1000,1000);
				}else{
					speed_mm_per_second_MasterWheel= CLAMP(speed_mm_per_second * xScale,-1000,1000);
					speed_mm_per_second_SlaveWheel = CLAMP(speed_mm_per_second,-1000,1000);
				}
		
			
			
			
			// Enable channel output
			SetEnable(enable);

			
			// Set output
			SetSpeed(speed_mm_per_second_MasterWheel);
			
			
			// Calculate inactivity timeout (Except, when charger is active -> keep device running)
			if (!chargeStateLowActive || ABS(speed_mm_per_second)>40){
				inactivity_timeout_counter = 0;
			}else{
				inactivity_timeout_counter++;
			}
			

		}
		
		// Decide if slave will be enabled
		enableSlave = (enable == SET && timedOut == RESET) ? SET : RESET;
		
		// Decide which process value has to be sent
		switch(sendSlaveIdentifier)
		{
			case 5:
				#ifdef TERMINAL_ENABLED_PID_TUNING
					sendSlaveValue = PID_PARAM_KP*10000.0;
					break;
				#else
					sendSlaveIdentifier=0;
				#endif
			case 6:
				#ifdef TERMINAL_ENABLED_PID_TUNING
					sendSlaveValue = PID_PARAM_KI*10000.0;
					break;
				#else
					sendSlaveIdentifier=0;
				#endif
			case 7:
				#ifdef TERMINAL_ENABLED_PID_TUNING
					sendSlaveValue = PID_PARAM_KD*10000.0;
					break;
				#else
					sendSlaveIdentifier=0;
				#endif
			case 0:
				sendSlaveValue = currentDC * 100;
				break;
			case 1:
				sendSlaveValue = batteryVoltage * 100;
				break;
			case 2:
				sendSlaveValue = realSpeed_mm_per_second * 1000;
				break;
			case 3:
				sendSlaveIdentifier++; //we jump case 3 since it is used just on navigator
			case 4:
				sendSlaveValue = remainingSteps;
				break;
			
			default:
				break;
		}
		//send data to slave board
		SendSlave(-speed_mm_per_second_SlaveWheel, enableSlave, RESET, chargeStateLowActive, sendSlaveIdentifier, sendSlaveValue);
		
		// Increment identifier
		sendSlaveIdentifier++;
		if (sendSlaveIdentifier > 7)
		{
			sendSlaveIdentifier = 0;
		}
		
		if((ABS(pitchAngle)>20) ||  (ABS(rollAngle)>20) ){
			robotReversed=TRUE;
			//actuatorSpeed=0;
			gpio_bit_write(LED_GREEN_PORT, LED_GREEN, RESET); //(inverted logic since it uses npn transistor)
		
			speed_mm_per_second=0;
			stopNavigator();
			ShutOff();
			
		}
		// Show green battery symbol when battery level BAT_LOW_LVL1 is reached
    if (batteryVoltage > BAT_LOW_LVL1)
		{
			// Show green battery light
			//ShowBatteryState(LED_GREEN); //green led is used by the actuator (blade motor) inside commsActuator.c
			
			// Beeps backwards
			BeepsBackwards(beepsBackwards);
		}
		// Make silent sound and show orange battery symbol when battery level BAT_LOW_LVL2 is reached
    else if (batteryVoltage > BAT_LOW_LVL2 && batteryVoltage < BAT_LOW_LVL1)
		{
			// Show orange battery light
			ShowBatteryState(LED_ORANGE);
			
      buzzerFreq = 5;
      buzzerPattern = 8;
    }
		// Make even more sound and show red battery symbol when battery level BAT_LOW_DEAD is reached
		else if  (batteryVoltage > BAT_LOW_DEAD && batteryVoltage < BAT_LOW_LVL2)
		{
			// Show red battery light
			ShowBatteryState(LED_RED);
			
      buzzerFreq = 5;
      buzzerPattern = 1;
    }
		// Shut device off, when battery is dead
		else if (batteryVoltage < BAT_LOW_DEAD)
		{
      ShutOff();
    }
		else
		{
			ShutOff();
    }

		if(panicButtonPressed==RESET){
			ShutOff();
    }
		
		// Shut device off when button is pressed
		if (gpio_input_bit_get(BUTTON_PORT, BUTTON_PIN))
		{
      while (gpio_input_bit_get(BUTTON_PORT, BUTTON_PIN)) {}
			ShutOff();
    }
		
		
		// Shut off device after INACTIVITY_TIMEOUT in minutes
    if (inactivity_timeout_counter > (INACTIVITY_TIMEOUT * 60 * 1000) / (DELAY_IN_MAIN_LOOP + 1))
		{ 
      ShutOff();
    }
#endif	
	

		Delay(DELAY_IN_MAIN_LOOP);
		
		// Reload watchdog (watchdog fires after 1,6 seconds)
		fwdgt_counter_reload();
  }
}

#ifdef MASTER
//----------------------------------------------------------------------------
// Turns the device off
//----------------------------------------------------------------------------
void ShutOff(void){
	int index = 0;
	buzzerPattern = 0;
	for (; index < 8; index++)
	{
		buzzerFreq = index;
		Delay(10);
	}
	buzzerFreq = 0;
	
	// Send shut off command to slave
	SendSlave(0, RESET, SET, RESET, RESET, RESET);
	
	// Disable usart
	usart_deinit(USART_MASTERSLAVE);
	
	// Set pwm and enable to off
	SetEnable(RESET);
	//SetPWM(0);
	speed_mm_per_second_MasterWheel=0;
	
	gpio_bit_write(SELF_HOLD_PORT, SELF_HOLD_PIN, RESET);
	while(1)
	{
		// Reload watchdog until device is off
		fwdgt_counter_reload();
	}
}

//----------------------------------------------------------------------------
// Shows the battery state on the LEDs
//----------------------------------------------------------------------------
void ShowBatteryState(uint32_t pin)
{
	#ifndef DEBUG_WITH_TRACE_ENABLED
		// gpio_bit_write(LED_GREEN_PORT, LED_GREEN, pin == LED_GREEN ? SET : RESET); //commented cause this pin is used to activate the motor with the blade of the lawnmower
		gpio_bit_write(LED_ORANGE_PORT, LED_ORANGE, pin == LED_ORANGE ? SET : RESET);
		gpio_bit_write(LED_RED_PORT, LED_RED, pin == LED_RED ? SET : RESET);
	#endif
}

//----------------------------------------------------------------------------
// Beeps while driving backwards
//----------------------------------------------------------------------------
void BeepsBackwards(FlagStatus beepsBackwards)
{
	// If the speed is less than -40, beep while driving backwards
	if (beepsBackwards == SET && speed_mm_per_second < -40)
	{
		buzzerFreq = 5;
    buzzerPattern = 4;
	}
	else
	{
		buzzerFreq = 0;
		buzzerPattern = 0;
	}
}
#endif

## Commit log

2019-05-12 RENAMED FOLDER
    [CommunicationOverview.ods, HoverBoard_SCHEMATIC_for_TAOTAO TT-SD2.2.sch, PIASTRA2D_EN.dwg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]
2019-05-26 updated schematic and smooth acceleration.
2019-07-29 accelerometer read
    introduced the reading of accelerometer chip to obtain roll and pich (and to shutdown the mower if someone tries to reverse it)
    [HoverBoard_SCHEMATIC_for_TAOTAO TT-SD2.2.sch, SerialProtocolDefinition.ods, SerialProtocolDefinition.xls]
2019-10-20 implemented perfect movements and wheels syncronization (still not perfect)
    implemented perfect movements and wheels syncronization (still not perfect)
    [SerialProtocolDefinition.ods, SerialProtocolDefinition.xls]
2020-08-18 restructured
    restructured.
    [0603 Capacitor.ipt, 0603 Resistor.ipt, Assembly1.0001.iam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]
2020-08-22 UPDATED IMAGES AND SCHEMATIC
